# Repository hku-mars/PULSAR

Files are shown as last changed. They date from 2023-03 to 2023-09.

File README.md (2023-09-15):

# PULSAR (powered-flying ultra-underactuated LiDAR sensing aerial robot)

## A self-rotating, single-actuated UAV with extended sensor field of view for autonomous navigation

**Paper Link**: https://www.science.org/doi/epdf/10.1126/scirobotics.ade4538

**Video Link**: https://www.youtube.com/watch?v=lrEJnJrRJsQ&t=218s

## 1 Structure CAD files

Including the CAD files of PULSAR and the swashplateless mechanism.

## 2 Hardware deisgn files

Including the hardware design files of the magnetic encoder (AS5600).

## 3 PX4 firmware of PULSAR

### 3.1 Hardware configuration
+ Power the magnetic encoder and config it using a I2C bus (please follow the AS5600 datasheet, you can use Arduino or Raspberry Pi or other devices you want, the encoder configuration is not involved in this PX4 firmware), and make sure the 910-Hz PWM signal is outputed (e.g., verified by a oscilloscope).
+ Connect the power port of magnetic encoder to a 5V port of the Pixhawk 4 Mini.
+ Connect the PWM signal of magnetic encoder to the CAP1 port of the Pixhawk 4 Mini.
+ Connect the ESC (off-the-shelf ESC is ok as long as it supports dshot protocol) to the MAIN OUT 1 port of the Pixhawk 4 Mini.

### 3.2 Software configuration
+ Clone the repository
+ Config your compile environment https://docs.px4.io/main/en/dev_setup/dev_env.html
+ Build the code and upload to Pixhawk 4 mini through USB connection
```
cd PULSAR
git submodule update --init
cd 3-PX4_Firmware/PULSAR_PX4
make px4_fmu-v5_default upload
```
+ Load the parameter file "PULSAR_PX4_parameters.params" to the Pixhawk 4 mini by QGroundControl or other tools (very important)
+ Keeping the USB connection, in the MAVLINK Console of QGroundControl, type
```
px4_cn start
```
+ If the encoder works well, two rotor angles (angle_compensated and angle_raw) will be printed in the MAVLINK terminal. Rotate the positive blade of the swashplateless mechanism to align with the negative direction of the body y axis of PULSAR (facing to LiDAR's front side, right hand side is the nevative y axis), and record the value of the printed "angle_raw". 
+ Modified the MACRO (SENSOR_ROTOR_ANGLE_BIAS) with the recorded value (see 3.2.2).
+ Compile the code and upload again.
+ Keeping the same blade's position and starting the angle print in MAVLINK again, make sure the "angle_compensated" is close to 0 deg or 360 deg.
+ To stop the print, type
```
px4_cn stop
```

### 3.3 Main modifications of the PX4 firmware

#### 3.3.1 PWM capture driver for magnetic encoder 
The files are located in "src/drivers/pwm_input". Please make sure that the encoder 910-Hz PWM signal is connected to the CAP1 of the Pixhawk 4 Mini. Changing the frequency should also modify the timer frequency in "PULSAR_PX4/src/drivers/pwm_input/pwm_input.cpp".

#### 3.3.2 Mixer of PULSAR
The mixer files are located in the "PULSAR_PX4/src/drivers/dshot/swashplateless".

SENSOR_ROTOR_ANGLE_BIAS (unit is degree) is used for compensating the encoder installation offset angle and it must be set properly.

MOTOR_DELAY_ANLGE_BIAS (unit is radian) is used for compensating the lag angle of the swashplateless mechanism. This value is different when using different motor or propeller and can be determined on a test stand with 6-axis force sensor by analyzing the moment data. If you use the propulsion system same as PULSAR (i.e., T-MOTOR MN5006 KV450 and MF1302 propeller), you don't need to change this value.

The data of swashplateless mechanism are published for logging.

#### 3.3.3 The repalcement of throttle output
The repalcement is conducted in "PULSAR_PX4/src/drivers/dshot/dshot.cpp".
Please make sure that the ESC signal wire is connected to the MAIN OUT1 of the Pixhawk 4 Mini. The dshot has been enabled if you had loaded the parameter file into the Pixhawk 4 mini.

#### 3.3.4 The attitude controller of PULSAR
The attitude controller is implemented in "PULSAR_PX4/src/modules/mc_att_control/AttitudeControl/AttitudeControl.cpp".
The attitude setpoint and feedback are published for data logging.

#### 3.3.5 The angular velocity controller of PULSAR
The angular velocity controller is implemented in "PULSAR_PX4/src/modules/sa_rate_control_me/sa_rate_control_me_main.cpp".
The angular velocity setpoint and feedback both in world frame are published for data logging.

#### 3.3.6 The position controller of PULSAR
There are some modifications in "PULSAR_PX4/src/modules/mc_pos_control" and "PULSAR_PX4/src/lib/flight_tasks".
This ensure the position command from remote controller (RC) is available in world frame rather than in body frame.

#### 3.3.7 Logging topics
Some ulog topics are added in "PULSAR_PX4/src/modules/logger/logged_topics.cpp" and "PULSAR_PX4/msg".

## 4 Software modules

### 4.1 FAST-LIO2 
Different from the standard version of FAST-LIO2, the FAST-LIO2 in this repository contains coordinate transformations of both odometry and point clouds because the LiDAR (Livox AVIA) is installed on PULSAR with a 90-degree rotated orientation. Refer to https://github.com/hku-mars/FAST_LIO for more configuration details.

To transmit the odometry from FAST-LIO2 to PX4, [MAVROS](https://github.com/mavlink/mavros) should be run with FAST-LIO2 at the same time
```
roslaunch mavros px4.launch
roslaunch fastlio mapping_avia_indoor.launch  # indoor environment
roslaunch fastlio mapping_avia_outdoor.launch  # outdoor environment
```

In addition, [Point-LIO](https://github.com/hku-mars/Point-LIO) is more suitable for PULSAR since it can handle higher self-rotation rate.

### 4.2 Planner
The new version of the planner used in PULSAR is in https://github.com/hku-mars/dyn_small_obs_avoidance.
Other planners can also be used for PULSAR if they can receive the odometry and point clouds provided by FAST-LIO2, Point-LIO, or other LIOs.

### 4.3 Incremental kd-forest
The incremental kd-forest is a data strcuture which contains many [ikd-trees](https://github.com/hku-mars/ikd-Tree).
You may contact [Yixi Cai](https://github.com/Ecstasy-EC) if there is any issue.

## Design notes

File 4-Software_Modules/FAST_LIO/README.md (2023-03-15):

## Related Works

1. [ikd-Tree](https://github.com/hku-mars/ikd-Tree): A state-of-art dynamic KD-Tree for 3D kNN search.
2. [IKFOM](https://github.com/hku-mars/IKFoM): A Toolbox for fast and high-precision on-manifold Kalman filter.
3. [UAV Avoiding Dynamic Obstacles](https://github.com/hku-mars/dyn_small_obs_avoidance): One of the implementation of FAST-LIO in robot's planning.
4. [R2LIVE](https://github.com/hku-mars/r2live): A high-precision LiDAR-inertial-Vision fusion work using FAST-LIO as LiDAR-inertial front-end.
5. [UGV Demo](https://www.youtube.com/watch?v=wikgrQbE6Cs): Model Predictive Control for Trajectory Tracking on Differentiable Manifolds.
6. [SC-A-LOAM](https://github.com/gisbi-kim/SC-A-LOAM#for-livox-lidar): A [Scan-Context](https://github.com/irapkaist/scancontext) loop closure module that can directly work with FAST-LIO1 (The support for FAST-LIO2 is under developing).

## FAST-LIO
**FAST-LIO** (Fast LiDAR-Inertial Odometry) is a computationally efficient and robust LiDAR-inertial odometry package. It fuses LiDAR feature points with IMU data using a tightly-coupled iterated extended Kalman filter to allow robust navigation in fast-motion, noisy or cluttered environments where degeneration occurs. Our package address many key issues:
1. Fast iterated Kalman filter for odometry optimization;
2. Automaticaly initialized at most steady environments;
3. Parallel KD-Tree Search to decrease the computation;

## FAST-LIO 2.0 (2021-07-05 Update)
<!-- ![image](doc/real_experiment2.gif) -->
<!-- [![Watch the video](doc/real_exp_2.png)](https://youtu.be/2OvjGnxszf8) -->
<div align="left">


</div>

**Related video:**  [FAST-LIO2](https://youtu.be/2OvjGnxszf8),  [FAST-LIO1](https://youtu.be/iYCY6T79oNU),  [FAST-LIO1 + Scan-context loop closure](https://youtu.be/Fw9S6D6HozA)

**Pipeline:**
<div align="center">

</div>

**New Features:**
1. Incremental mapping using [ikd-Tree](https://github.com/hku-mars/ikd-Tree), achieve faster speed and over 100Hz LiDAR rate.
2. Direct odometry (scan to map) on Raw LiDAR points (feature extraction can be closed), achieving better accuracy.
3. Since no need for feature extraction, FAST-LIO2 can support different LiDAR Types including spinning (Velodyne, Ouster) and solid-state (Avia, horizon) LiDARs, and can be easily extended to support more LiDAR.
4. Support external IMU.
5. Support ARM-based platforms including Khadas VIM3, Nivida TX2, Raspberry Pi 4B(8G RAM).

**Related papers**: 

[FAST-LIO2: Fast Direct LiDAR-inertial Odometry](doc/Fast_LIO_2.pdf)

[FAST-LIO: A Fast, Robust LiDAR-inertial Odometry Package by Tightly-Coupled Iterated Kalman Filter](https://arxiv.org/abs/2010.08196)

**Contributors**

[Wei Xu 徐威](https://github.com/XW-HKU)，[Yixi Cai 蔡逸熙](https://github.com/Ecstasy-EC)，[Dongjiao He 贺东娇](https://github.com/Joanna-HE)，[Fangcheng Zhu 朱方程](https://github.com/zfc-zfc)，[Jiarong Lin 林家荣](https://github.com/ziv-lin)，[Zheng Liu 刘政](https://github.com/Zale-Liu), [Borong Yuan](https://github.com/borongyuan)

<!-- <div align="center">
    <img src="doc/results/HKU_HW.png" width = 49% >
    <img src="doc/results/HKU_MB_001.png" width = 49% >
</div> -->

## 1. Prerequisites
### 1.1 **Ubuntu** and **ROS**
**Ubuntu >= 16.04**

For **Ubuntu 18.04 or higher**, the **default** PCL and Eigen is enough for FAST-LIO to work normally.

ROS    >= Melodic. [ROS Installation](http://wiki.ros.org/ROS/Installation)

### 1.2. **PCL && Eigen**
PCL    >= 1.8,   Follow [PCL Installation](http://www.pointclouds.org/downloads/linux.html).

Eigen  >= 3.3.4, Follow [Eigen Installation](http://eigen.tuxfamily.org/index.php?title=Main_Page).

### 1.3. **livox_ros_driver**
Follow [livox_ros_driver Installation](https://github.com/Livox-SDK/livox_ros_driver).

*Remarks:*
- Since the FAST-LIO must support Livox serials LiDAR firstly, so the **livox_ros_driver** must be installed and **sourced** before run any FAST-LIO luanch file.
- How to source? The easiest way is add the line ``` source $Licox_ros_driver_dir$/devel/setup.bash ``` to the end of file ``` ~/.bashrc ```, where ``` $Licox_ros_driver_dir$ ``` is the directory of the livox ros driver workspace (should be the ``` ws_livox ``` directory if you completely followed the livox official document).

## 2. Build
Clone the repository and catkin_make:

```
    cd ~/$A_ROS_DIR$/src
    git clone https://github.com/hku-mars/FAST_LIO.git
    cd FAST_LIO
    git submodule update --init
    cd ../..
    catkin_make
    source devel/setup.bash
```
- Remember to source the livox_ros_driver before build (follow 1.3 **livox_ros_driver**)
- If you want to use a custom build of PCL, add the following line to ~/.bashrc
```export PCL_ROOT={CUSTOM_PCL_PATH}```
## 3. Directly run

Please make sure the IMU and LiDAR are **Synchronized**, that's important.
### 3.1 For Avia
Connect to your PC to Livox Avia LiDAR by following  [Livox-ros-driver installation](https://github.com/Livox-SDK/livox_ros_driver), then
```
    cd ~/$FAST_LIO_ROS_DIR$
    source devel/setup.bash
    roslaunch fast_lio mapping_avia.launch
    roslaunch livox_ros_driver livox_lidar_msg.launch
```
- For livox serials, FAST-LIO only support the data collected by the ``` livox_lidar_msg.launch ``` since only its ``` livox_ros_driver/CustomMsg ``` data structure produces the timestamp of each LiDAR point which is very important for the motion undistortion. ``` livox_lidar.launch ``` can not produce it right now.
- If you want to change the frame rate, please modify the **publish_freq** parameter in the [livox_lidar_msg.launch](https://github.com/Livox-SDK/livox_ros_driver/blob/master/livox_ros_driver/launch/livox_lidar_msg.launch) of [Livox-ros-driver](https://github.com/Livox-SDK/livox_ros_driver) before make the livox_ros_driver pakage.

### 3.2 For Livox serials with external IMU

mapping_avia.launch theratically supports mid-70, mid-40 or other livox serial LiDAR, but need to setup some parameters befor run:

Edit ``` config/avia.yaml ``` to set the below parameters:

1. LiDAR point cloud topic name: ``` lid_topic ```
2. IMU topic name: ``` imu_topic ```
3. Translational extrinsic: ``` extrinsic_T ```
4. Rotational extrinsic: ``` extrinsic_R ``` (only support rotation matrix)
- The extrinsic parameters in FAST-LIO is defined as the LiDAR's pose (position and rotation matrix) in IMU body frame (i.e. the IMU is the base frame). They can be found in the official manual.
- FAST-LIO produces a very simple software time sync for livox LiDAR, set parameter ```time_sync_en``` to ture to turn on. But turn on **ONLY IF external time synchronization is really not possible**, since the software time sync cannot make sure accuracy.

### 3.3 For Velodyne or Ouster (Velodyne as an example)

Step A: Setup before run

Edit ``` config/velodyne.yaml ``` to set the below parameters:

1. LiDAR point cloud topic name: ``` lid_topic ```
2. IMU topic name: ``` imu_topic ``` (both internal and external, 6-aixes or 9-axies are fine)
3. Line number (we tested 16 and 32 line, but not tested 64 or above): ``` scan_line ```
4. Translational extrinsic: ``` extrinsic_T ```
5. Rotational extrinsic: ``` extrinsic_R ``` (only support rotation matrix)
- The extrinsic parameters in FAST-LIO is defined as the LiDAR's pose (position and rotation matrix) in IMU body frame (i.e. the IMU is the base frame).

Step B: Run below
```
    cd ~/$FAST_LIO_ROS_DIR$
    source devel/setup.bash
    roslaunch fast_lio mapping_velodyne.launch
```

Step C: Run LiDAR's ros driver or play rosbag.

*Remarks:*
- We will produce some velodyne datasets which is already transfered to Rosbags, please wait for a while.

### 3.4 PCD file save

Set ``` pcd_save_enable ``` in launchfile to ``` 1 ```. All the scans (in global frame) will be accumulated and saved to the file ``` FAST_LIO/PCD/scans.pcd ``` after the FAST-LIO is terminated. ```pcl_viewer scans.pcd``` can visualize the point clouds.

*Tips for pcl_viewer:*
- change what to visualize/color by pressing keyboard 1,2,3,4,5 when pcl_viewer is running. 
```
    1 is all random
    2 is X values
    3 is Y values
    4 is Z values
    5 is intensity
```

## 4. Rosbag Example
### 4.1 Indoor rosbag (Livox Avia LiDAR)

<div align="center"><img src="doc/results/HKU_LG_Indoor.png" width=100% /></div>

Download [avia_indoor_quick_shake_example1](https://drive.google.com/file/d/1SWmrwlUD5FlyA-bTr1rakIYx1GxS4xNl/view?usp=sharing) or [avia_indoor_quick_shake_example2](https://drive.google.com/file/d/1wD485CIbzZlNs4z8e20Dv2Q1q-7Gv_AT/view?usp=sharing) and then
```
roslaunch fast_lio mapping_avia.launch
rosbag play YOUR_DOWNLOADED.bag

```

### 4.2 Outdoor rosbag (Livox Avia LiDAR)

<div align="center"><img src="doc/results/HKU_MB_002.png" width=100% /></div>

<!-- <div align="center"><img src="doc/results/mid40_outdoor.png" width=90% /></div> -->

Download [avia_hku_main building_mapping](https://drive.google.com/file/d/1GSb9eLQuwqmgI3VWSB5ApEUhOCFG_Sv5/view?usp=sharing) and then
```
roslaunch fast_lio mapping_avia.launch
rosbag play YOUR_DOWNLOADED.bag
```

## 5.Implementation on UAV
In order to validate the robustness and computational efficiency of FAST-LIO in actual mobile robots, we build a small-scale quadrotor which can carry a Livox Avia LiDAR with 70 degree FoV and a DJI Manifold 2-C onboard computer with a 1.8 GHz Intel i7-8550U CPU and 8 G RAM, as shown in below.

The main structure of this UAV is 3d printed (Aluminum or PLA), the .stl file will be open-sourced in the future.

<div align="center">
    <img src="doc/uav01.jpg" width=40.5% >
    <img src="doc/uav_system.png" width=57% >
</div>

## 6.Acknowledgments

Thanks for LOAM(J. Zhang and S. Singh. LOAM: Lidar Odometry and Mapping in Real-time), [Livox_Mapping](https://github.com/Livox-SDK/livox_mapping), [LINS](https://github.com/ChaoqinRobotics/LINS---LiDAR-inertial-SLAM) and [Loam_Livox](https://github.com/hku-mars/loam_livox).

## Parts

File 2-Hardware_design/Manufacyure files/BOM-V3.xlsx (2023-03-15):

Comment | Description | Designator | Footprint | LibRef | Quantity
1uF (105) 10% 50V | 贴片电容 | C1, C3 | 0603_C | 0603 1uF (105) 10% 50V | 2
10uF (106) 10% 10V | 贴片电容 | C2 | 0603_C | 0603 10uF (106) 10% 10V | 1
ports_5 |  | J1 | GH1.25-LS-5P | ports_5 | 1
10KΩ (1002) ±1% | 贴片电阻 | R1, R2 | 0603_R | 0603 10KΩ (1002) 1% | 2
1KΩ (1001) ±1% | 贴片电阻 | R3 | 0603_R | 0603 1KΩ (1001) 1% | 1
SHORT-2PIN |  | S1 | SHORT-2PIN | SHORT-2PIN | 1
AS5600 | Magnet Encoder | U1 | SOIC127P600X175-8N | AS5600 | 1

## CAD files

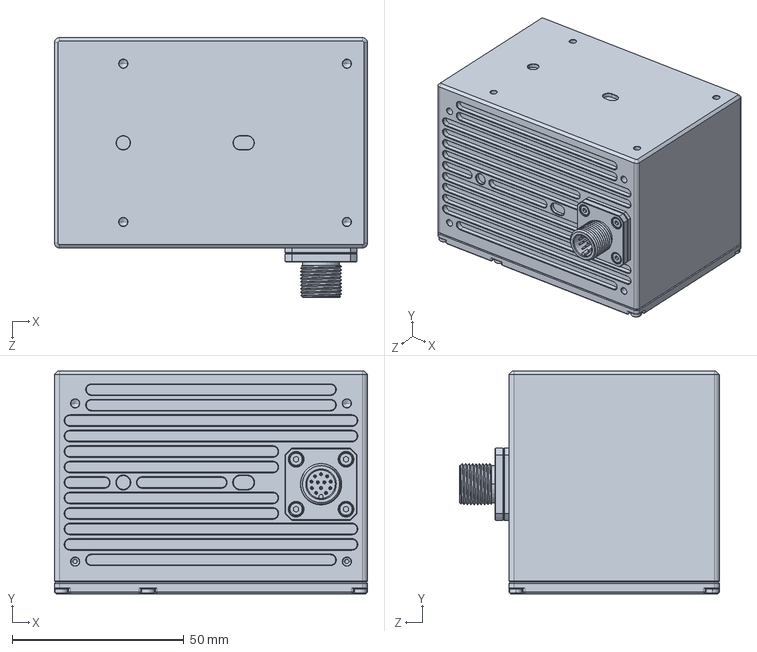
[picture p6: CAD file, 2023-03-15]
1-Structure_CAD/PULSAR/LIVOX_AVIA.SLDPRT
91.0 x 64.8 x 75.6 mm

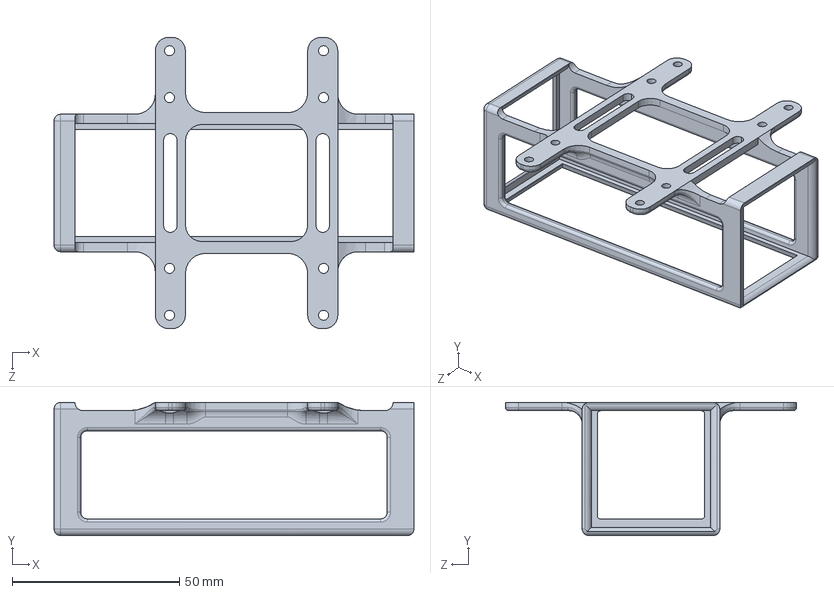
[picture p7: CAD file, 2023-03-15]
1-Structure_CAD/PULSAR/lower_structure/Battery_hold-lateral-V2.SLDPRT
107.5 x 39.8 x 87.0 mm

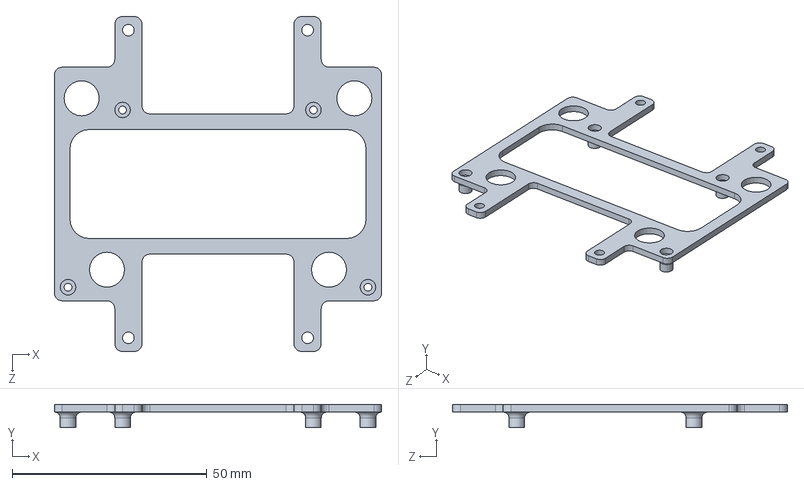
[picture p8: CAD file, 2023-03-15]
1-Structure_CAD/PULSAR/upper_structure/computer_holder.SLDPRT
84.0 x 6.00 x 86.0 mm

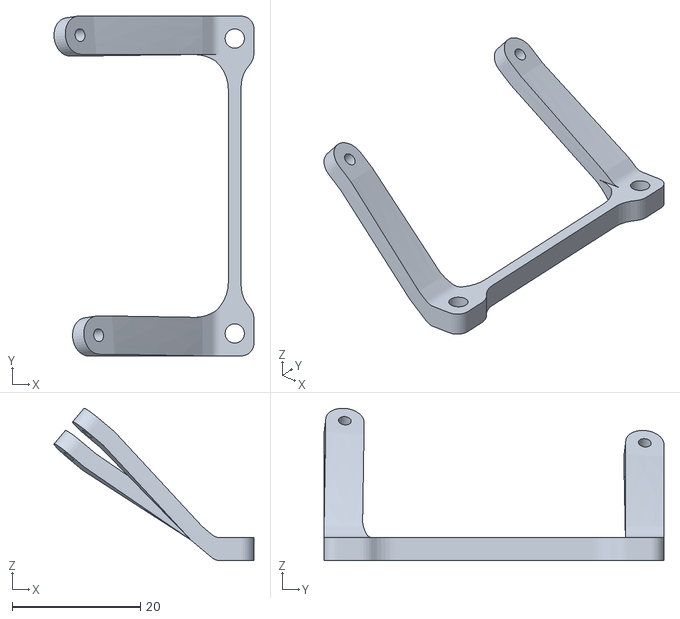
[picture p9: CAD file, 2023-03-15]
1-Structure_CAD/PULSAR/vanes_structure/vanes_holder_connector_short.STL
31.2 x 53.0 x 23.8

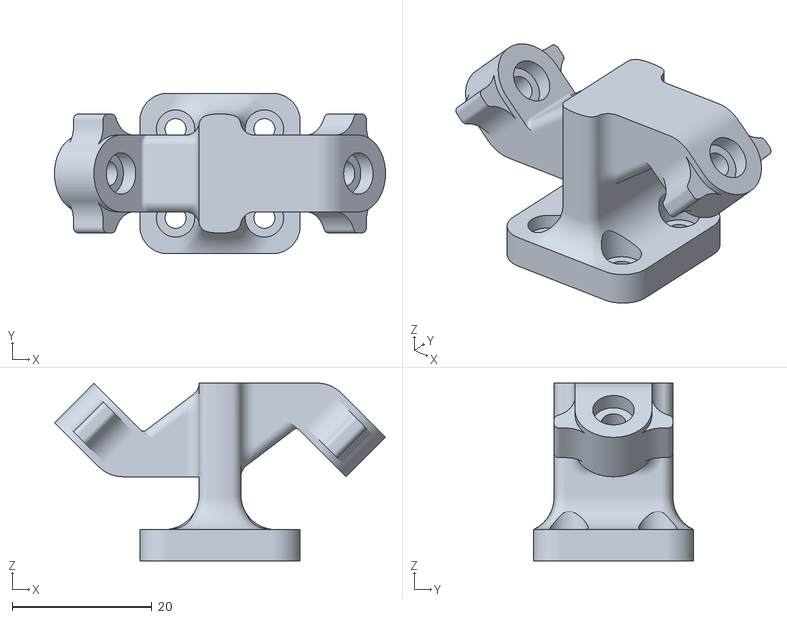
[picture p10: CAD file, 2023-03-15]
1-Structure_CAD/Swashplateless mechanism/Central_hub.STL
47.4 x 23.0 x 25.5

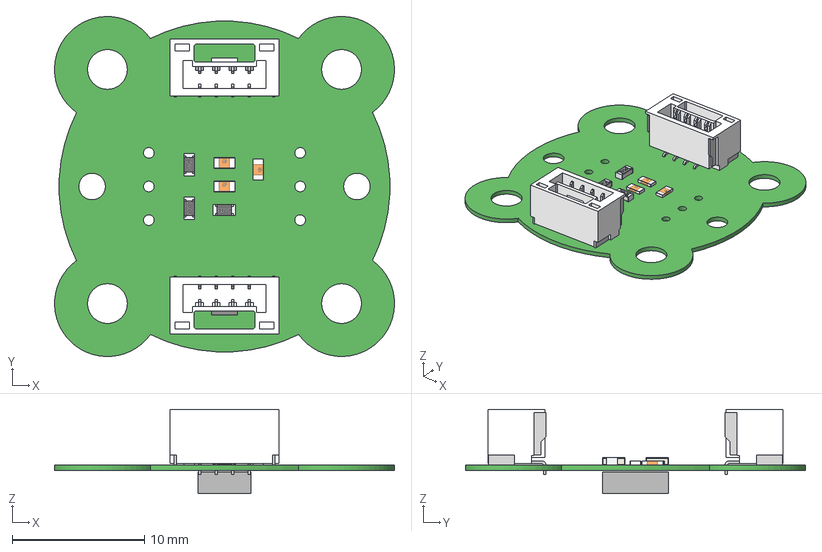
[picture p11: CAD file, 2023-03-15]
2-Hardware_design/V1.step
25.7 x 25.7 x 6.36 mm
Board
Extruded
User_Library-RES_1609-0603 x 3
A1257WR-S-4P x 2
User_Library-0603_SMD_Capacitor x 3

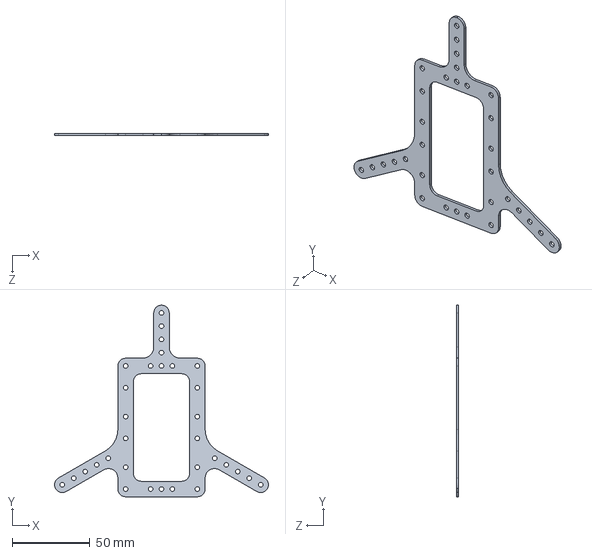
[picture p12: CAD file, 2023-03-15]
1-Structure_CAD/PULSAR/lower_structure/body_support-fiber-V2.SLDPRT
137.3 x 123.0 x 1.50 mm

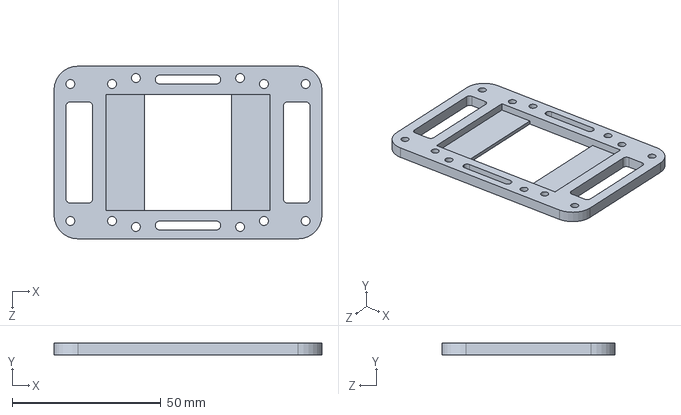
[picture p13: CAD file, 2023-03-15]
1-Structure_CAD/PULSAR/upper_structure/px4_holder.SLDPRT
90.0 x 4.00 x 58.0 mm

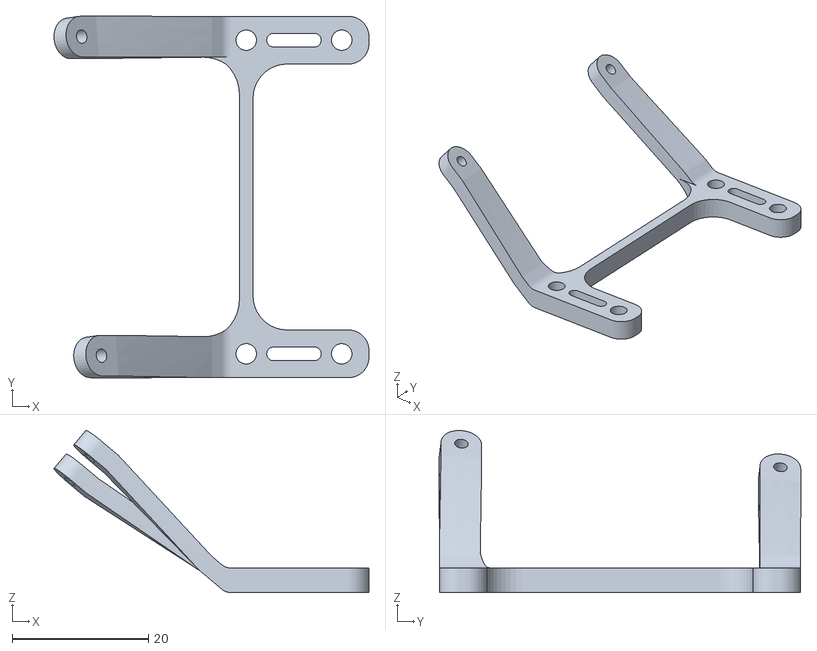
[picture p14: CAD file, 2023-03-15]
1-Structure_CAD/PULSAR/vanes_structure/vanes_holder_connector_long.STL
46.2 x 53.0 x 23.8

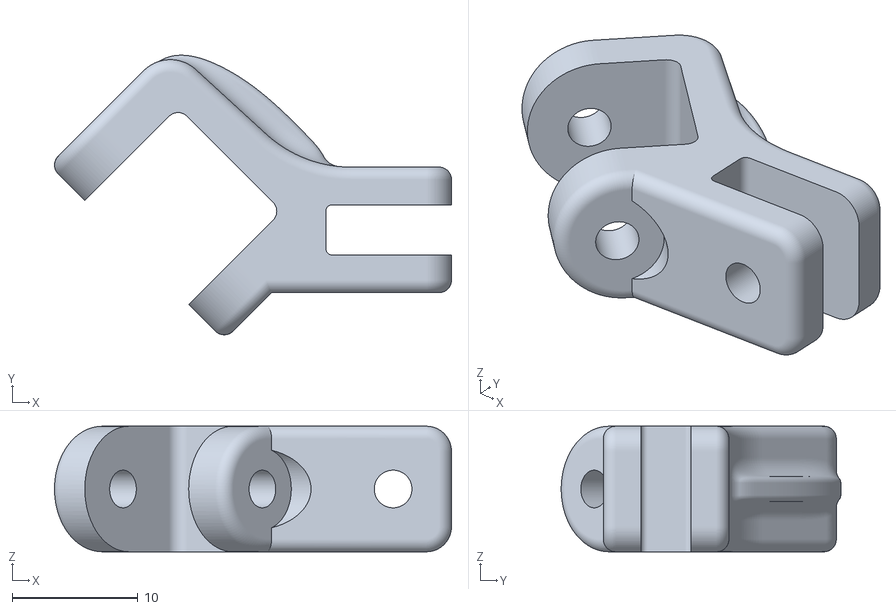
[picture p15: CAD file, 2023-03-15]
1-Structure_CAD/Swashplateless mechanism/Side_hub.STL
31.6 x 22.3 x 10.0

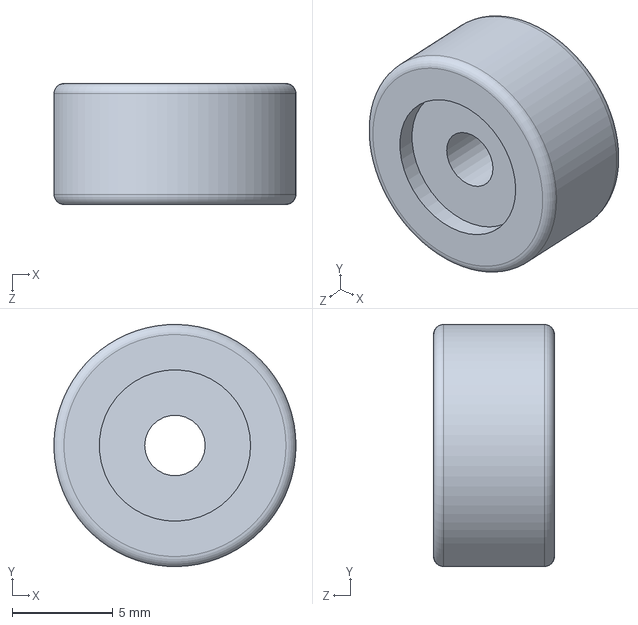
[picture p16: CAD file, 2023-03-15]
1-Structure_CAD/PULSAR/lower_structure/12x6_wheel.SLDPRT
12.0 x 12.0 x 6.00 mm

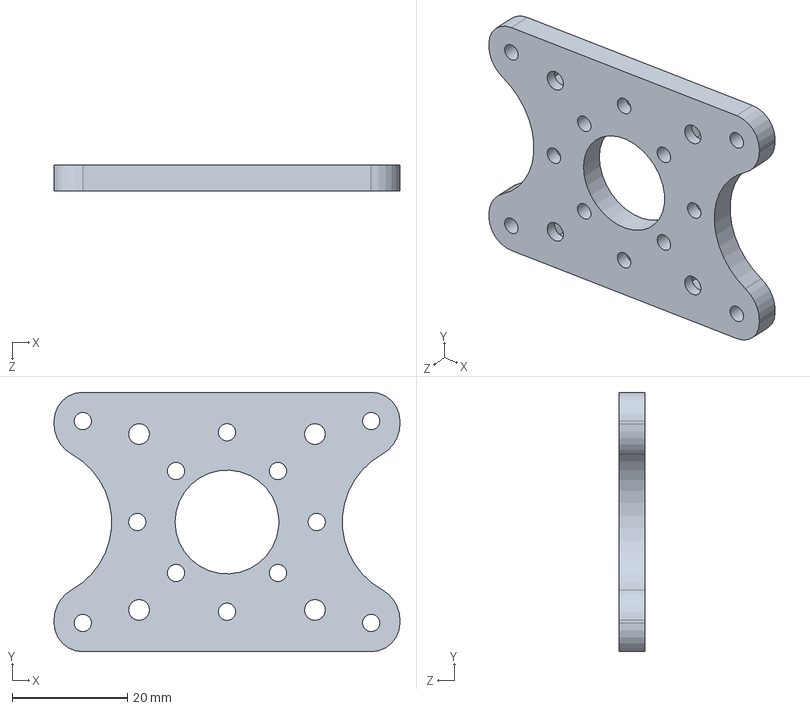
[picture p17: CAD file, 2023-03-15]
1-Structure_CAD/PULSAR/upper_structure/motor_holder.SLDPRT
60.0 x 45.0 x 4.50 mm

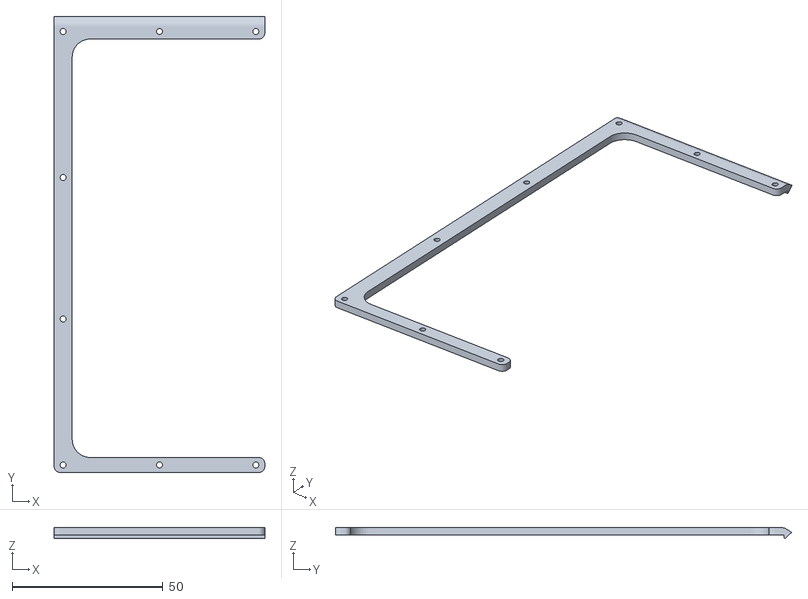
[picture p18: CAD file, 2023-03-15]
1-Structure_CAD/PULSAR/vanes_structure/vanes_holder.STL
70.0 x 151.5 x 3.60

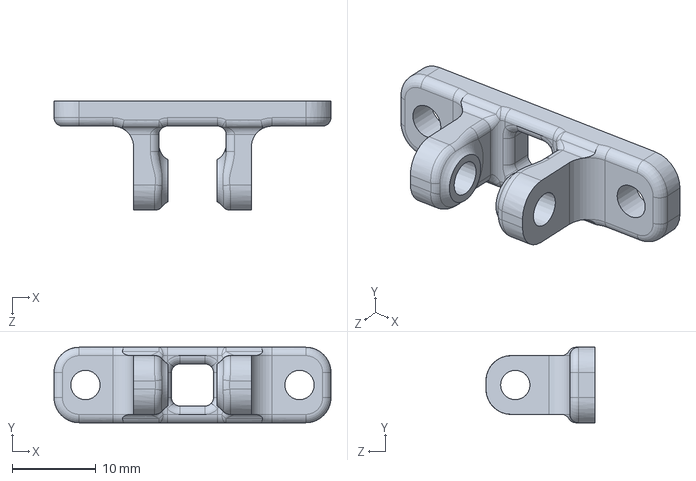
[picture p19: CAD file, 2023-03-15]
1-Structure_CAD/PULSAR/lower_structure/wheel_holder-V2.SLDPRT
33.0 x 9.00 x 13.0 mm

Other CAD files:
1-Structure_CAD/PULSAR/lower_structure/Battery_hold-lateral-V2.STL
1-Structure_CAD/PULSAR/lower_structure/body_support-fiber-V2.DXF
1-Structure_CAD/PULSAR/lower_structure/wheel_holder-V2.STL
1-Structure_CAD/PULSAR/upper_structure/computer_holder.STL
1-Structure_CAD/PULSAR/upper_structure/motor_holder.STL
1-Structure_CAD/PULSAR/upper_structure/px4_holder.STL
2-Hardware_design/V1.SLDASM

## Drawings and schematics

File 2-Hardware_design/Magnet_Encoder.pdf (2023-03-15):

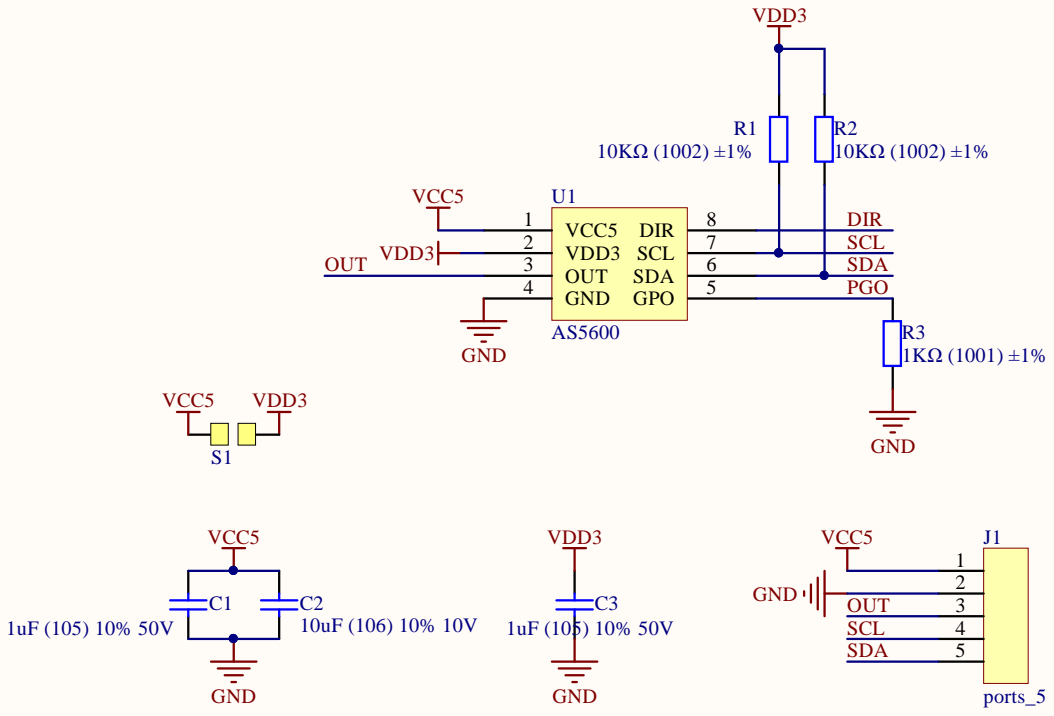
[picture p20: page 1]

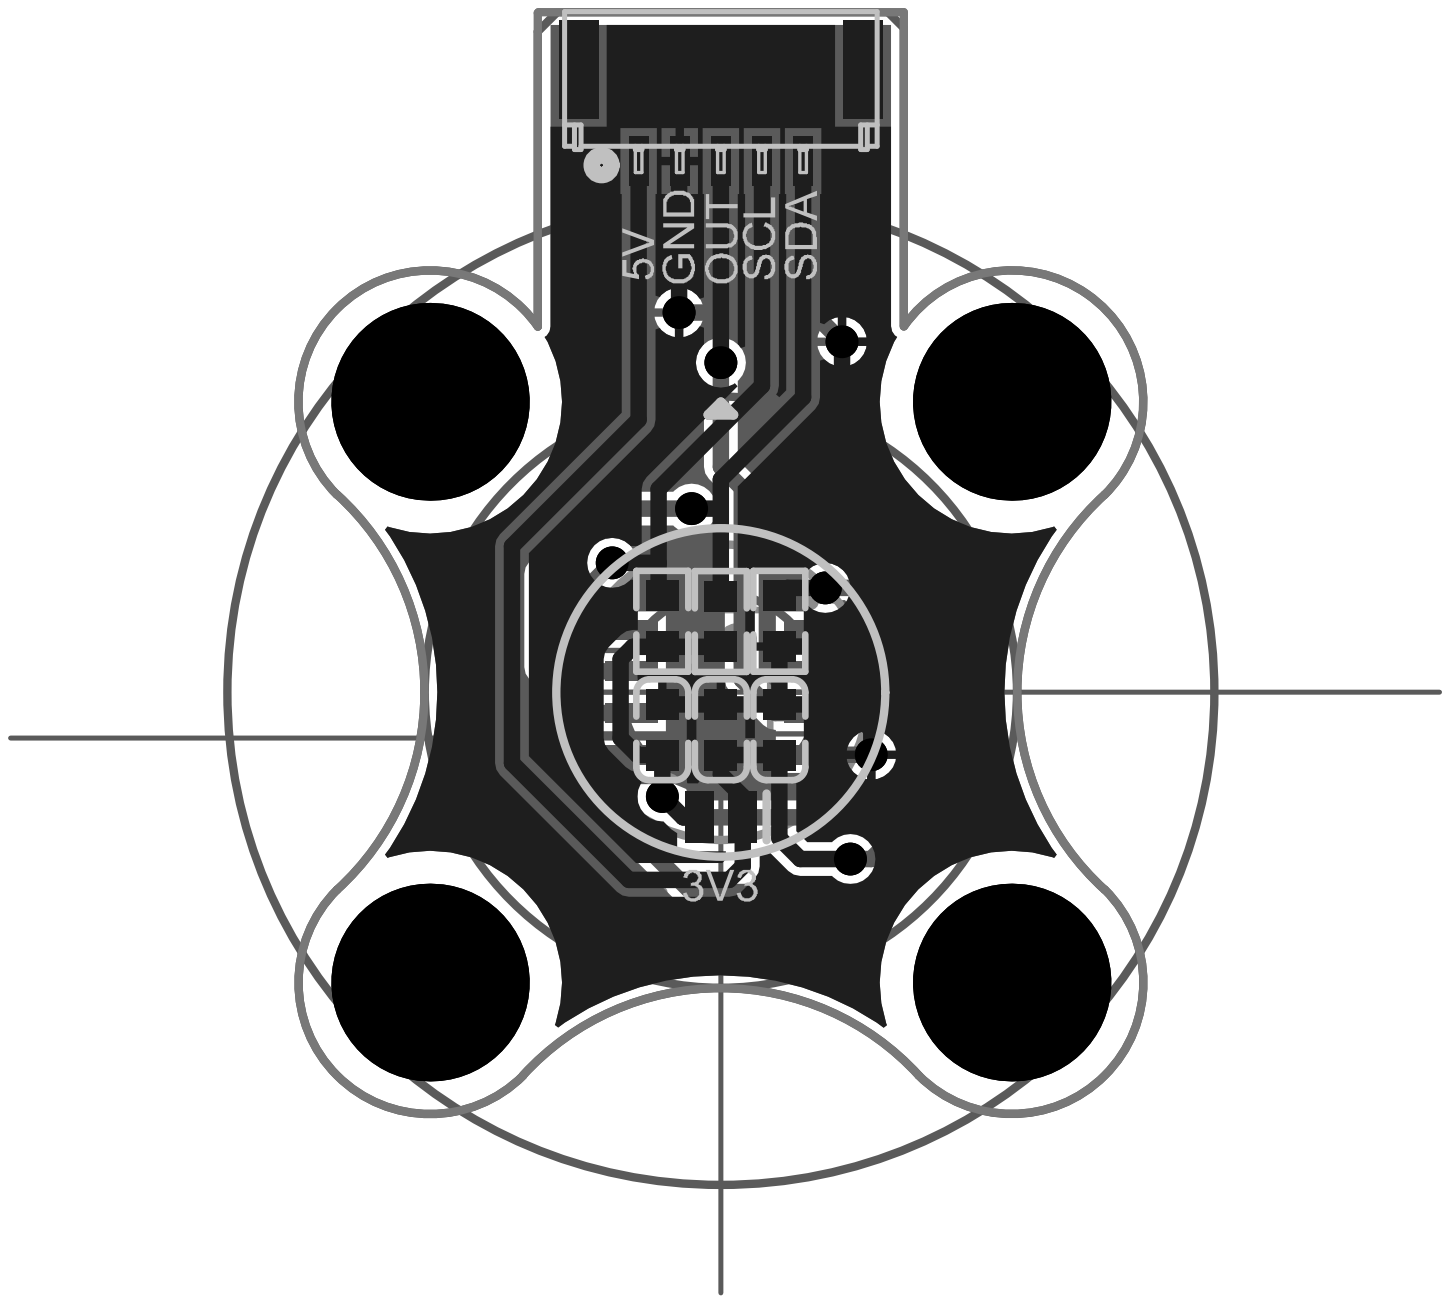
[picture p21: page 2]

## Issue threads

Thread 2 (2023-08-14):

Assembly file is empty. Majority of the CAD files for PULSAR were not included

Rotoslider, 2023-08-14:
Cad files are incomplete. Assembly file is empty. You must use pack and go to save all files associated with assembly or it will fail like this.

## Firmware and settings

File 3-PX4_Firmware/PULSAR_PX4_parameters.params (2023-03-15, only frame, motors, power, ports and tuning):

1	1	BAT1_A_PER_V	36.367515563964843750	9
1	1	BAT1_CAPACITY	1850.000000000000000000	9
1	1	BAT1_I_CHANNEL	-1	6
1	1	BAT1_N_CELLS	6	6
1	1	BAT1_R_INTERNAL	-1.000000000000000000	9
1	1	BAT1_SOURCE	0	6
1	1	BAT1_V_CHANNEL	-1	6
1	1	BAT1_V_CHARGED	4.199999809265136719	9
1	1	BAT1_V_DIV	18.082136154174804688	9
1	1	BAT1_V_EMPTY	3.400000095367431641	9
1	1	BAT1_V_LOAD_DROP	0.300000011920928955	9
1	1	BAT2_A_PER_V	36.367515563964843750	9
1	1	BAT2_CAPACITY	-1.000000000000000000	9
1	1	BAT2_I_CHANNEL	-1	6
1	1	BAT2_N_CELLS	0	6
1	1	BAT2_R_INTERNAL	-1.000000000000000000	9
1	1	BAT2_SOURCE	-1	6
1	1	BAT2_V_CHANNEL	-1	6
1	1	BAT2_V_CHARGED	4.050000190734863281	9
1	1	BAT2_V_DIV	18.100000381469726563	9
1	1	BAT2_V_EMPTY	3.500000000000000000	9
1	1	BAT2_V_LOAD_DROP	0.300000011920928955	9
1	1	BAT_ADC_CHANNEL	-1	6
1	1	BAT_A_PER_V	36.367515563964843750	9
1	1	BAT_CAPACITY	1850.000000000000000000	9
1	1	BAT_CRIT_THR	0.070000000298023224	9
1	1	BAT_EMERGEN_THR	0.050000000745058060	9
1	1	BAT_LOW_THR	0.150000005960464478	9
1	1	BAT_N_CELLS	6	6
1	1	BAT_R_INTERNAL	-1.000000000000000000	9
1	1	BAT_SOURCE	0	6
1	1	BAT_V_CHARGED	4.199999809265136719	9
1	1	BAT_V_DIV	18.082136154174804688	9
1	1	BAT_V_EMPTY	3.400000095367431641	9
1	1	BAT_V_LOAD_DROP	0.300000011920928955	9
1	1	BAT_V_OFFS_CURR	0.000000000000000000	9
1	1	MC_PITCHRATE_D	0.000000000000000000	9
1	1	MC_PITCHRATE_FF	0.000000000000000000	9
1	1	MC_PITCHRATE_I	0.159999996423721313	9
1	1	MC_PITCHRATE_K	1.000000000000000000	9
1	1	MC_PITCHRATE_MAX	220.000000000000000000	9
1	1	MC_PITCHRATE_P	0.360000014305114746	9
1	1	MC_PITCH_P	17.000000000000000000	9
1	1	MC_ROLLRATE_D	0.000000000000000000	9
1	1	MC_ROLLRATE_FF	0.000000000000000000	9
1	1	MC_ROLLRATE_I	0.159999996423721313	9
1	1	MC_ROLLRATE_K	1.000000000000000000	9
1	1	MC_ROLLRATE_MAX	220.000000000000000000	9
1	1	MC_ROLLRATE_P	0.360000014305114746	9
1	1	MC_ROLL_P	17.000000000000000000	9
1	1	MC_YAWRATE_D	0.000000000000000000	9
1	1	MC_YAWRATE_FF	0.000000000000000000	9
1	1	MC_YAWRATE_I	0.100000001490116119	9
1	1	MC_YAWRATE_K	1.000000000000000000	9
1	1	MC_YAWRATE_MAX	200.000000000000000000	9
1	1	MC_YAWRATE_P	0.200000002980232239	9
1	1	MC_YAW_P	2.799999952316284180	9
1	1	MC_YAW_WEIGHT	0.400000005960464478	9
1	1	MOT_ORDERING	0	6
1	1	MOT_POLE_COUNT	14	6
1	1	MOT_SLEW_MAX	0.000000000000000000	9
1	1	SYS_AUTOSTART	4031	6
